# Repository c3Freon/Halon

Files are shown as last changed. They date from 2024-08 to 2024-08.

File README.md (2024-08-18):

# Halon 3D-Printer
## What is Halon
Halon is my 3D-Printer design. Its an small self containt portable high speed FDM 3D-Printer.
I designed this priter to be my travel printer for events and as an rabbit prototyping printer.

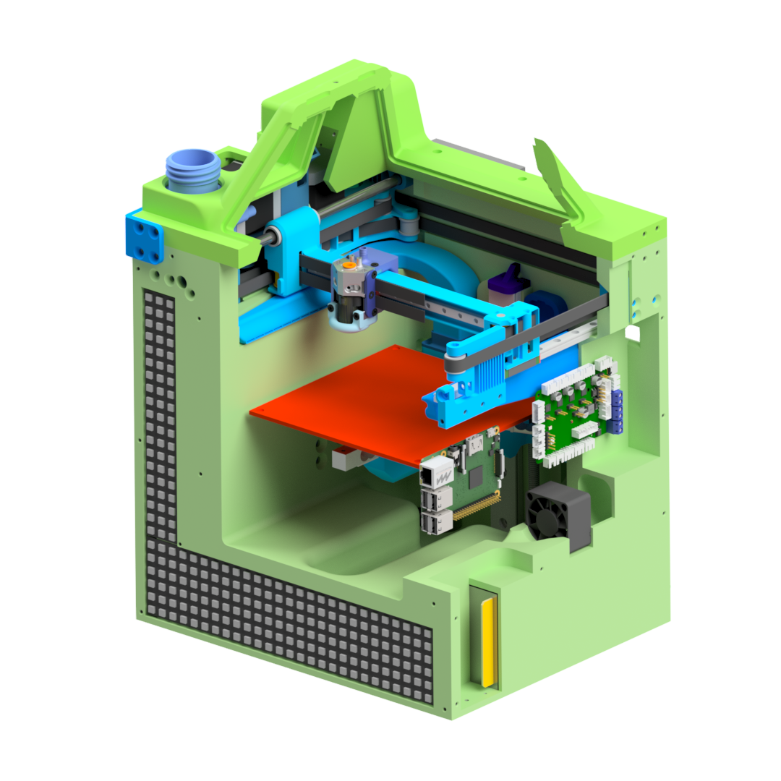
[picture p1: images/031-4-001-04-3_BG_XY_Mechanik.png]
3D-Render of the first Prototype


## Design Targets
1. The Printer should be usable as an praktical 3D-Printer
2. The Printer should be Self Containt. No external spool, no external power supply and an compleate printer enclosure.
3. The Printer should be as fast as possible. An design goal of 1m/s velocity and 100m/s² has been set.
4. The Printer should be buildable with standard mashiens avavible in moast Hackspaces/Makerspaces.

# Prototype
This Project started in autum 2023 as an studing project. I have developed the prototype over an halve jear and i build the prototype. On the GPN22 i presented the prototype. Because of the interest and feedback on the event, i decided to publish the design of printer so more people can build this design. 

https://github.com/user-attachments/assets/4c1e7ec1-202b-4d33-9429-380821325e8d

The mechanics of the prototype function as Planned. It reaches an maximum speed of 0.5m/s with an acceleration of 100m/s² reliable without stepp loss. Even at this high acceleration the ringing on the axis is minimal. 
The print cooling system is sufficient even on maximum print speed. But, the prototype uses two 15mm turbines for the side cooling and an compressor for the head part cooling. Both are extremly loud (operator needs ear protection when opening the enclosure) which violates the first design target.
The extrusion system is currently the speed limiting factor on this mashien. The prototype uses an Creality K1 Hotend and an dual gear browden extruder. Its currently limited to 30mm³/s. The hotend and the XY motors get cooled by an water cooling loop.

The Prototype was first designed to be mostly printed on the university SLS Printer. So some Parts arent optimised for more Accesseble Printing methodes. The hotend heatsink designed to be manufactured from aluminium with an SLM Printer.

Intermediate build state of the printer Where many aspects are visible and the cabeling horror hasnt begun

## Technical specifications
- Maximum speed 500mm/s at 100m/s² acceleration
- Print area 150x150x120mm
- Machine size 297x240x430mm
- Encapsulated print area
- Water cooled print head
- Acceleration sensor for input shaper
- Fillament spool integrated in printer
- Integrated active fillament drying box (maximum 70°C with fan)
- Charcoal filter with fan
- Auto-levelling via load cells under the print bed
- Rigid print bed
- Strong side cooling
- Rigid axle design for low ringing
- Klipper firmware
- Clog-free Y-axis guide

## Electronics
Two Bigtreetech skr pico control boards, two Raspberrypi picos and a Raspberrypi 4 were used to control the prototype. Two Bigtreetech TMC5160T Plus driver boards with a supply voltage of 48V were used for the stepper motors. A used server power supply was used as the power supply, providing 12V with a maximum output of 450W. Two boost converters are used to generate a 24V and a 48V rail from the 12V power supply. The first skr Pico control board is powered by the 24V and drives the stepper motors for the E and Z axes. It also drives the hot end heaters and some of the fans. The second SKR Pico control board is supplied with 12V. This board controls the heating bed and the drying box heating. The 48V stepper motor drivers are controlled by the first Rasperrypi Pico. The second pico is not connected to the Klipper. It reads the load cells under the bed and simulates a BL-Touch for automatic bed levelling to the controller.

## What works well
The printer's motion system works as designed. The printer achieves a positioning speed of 0.5m/s with an acceleration of 100m/s². The rigid axis structure means that even at these extreme settings, ringing is very low.
The cantilevered Z-axis is very rigid due to the rigid guide and wide beam.
Automatic levelling via load cells under the print bed is reliable and accurate.
The printer setup with a large print enclosure works.

https://github.com/user-attachments/assets/8164ebac-18e3-453c-8e3b-d6f8cc71612e

## What is still bad
A few problems were discovered with the first prototype. Firstly, water cooling will not be installed in future versions. The improved printhead cooling provided by water cooling does not justify the significantly increased maintenance and space requirements of water cooling. On the one hand, the cooling water has to be refilled every few days if silicone hoses are used. On the other hand, the tightness of the system is a problem. My prototype is currently leaking because the water tank has cracked due to the high pressure chamber temperatures.
Secondly, the extrusion system of the current printer is still suboptimal. In the prototype, the filament tube is bent too tightly in some places, causing high friction in the filament tube. In addition, the extruder cuts through the fillament when overloaded, which still happens too often due to the high friction in the system. 
The hot end is the limiting factor for print speed in the prototype.
When I designed the electronics, I didn't know about the Bigtreetech Kraken board. This would have simplified the electronics considerably. 
The side cooling fans can effectively cool the print even at maximum speed. However, the fans are so loud at maximum speed that ear protection is required next to the machine. The same applies to the compressed air cooling of the parts. This uses a piston compressor. However, this has a very high pressure pulsation, which also makes it very loud.
In addition, the heat generated by the stepper motors and voltage converters was underestimated during the design phase, which meant that fans had to be added to the prototypes at a later stage.

# Version 2
In the second version of the Halon printer I would like to fix the bugs of the first version. The following optimizations are planned:
- Replacing the water cooling of the print head with compressed air cooling (less maintenance)
- Upgrading the print head to a Mellow Goliath (higher volume flow)
- Modification of the extruder design (higher reliability, i have an high grip three wheel extuder design in the works)
- Use of a CPap fan for part cooling (noise reduction)
- Use of large radial fans for additional cooling (noise reduction)
- Modification of the control board to a Bigtreetech kraken
- Optimization of the housing design (improved assembly)

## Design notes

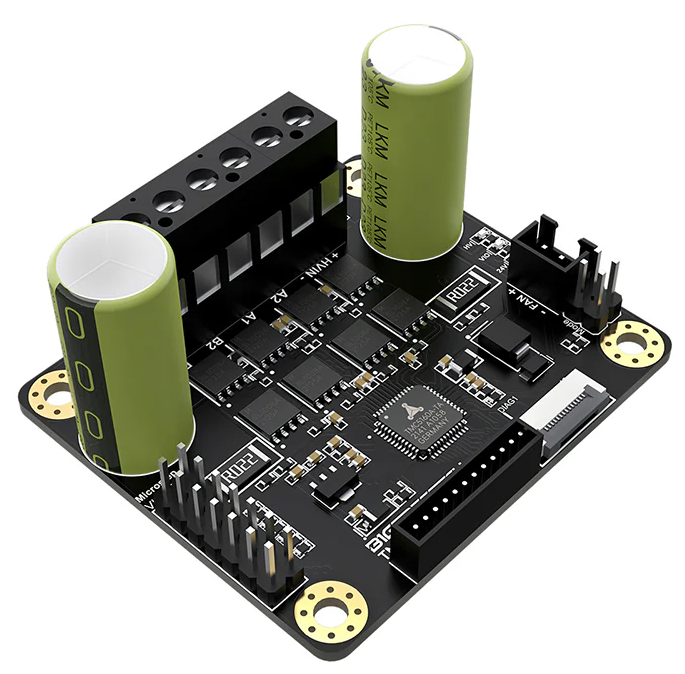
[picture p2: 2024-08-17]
images/Wiki/03_Pictures/08_MotorDriver.png

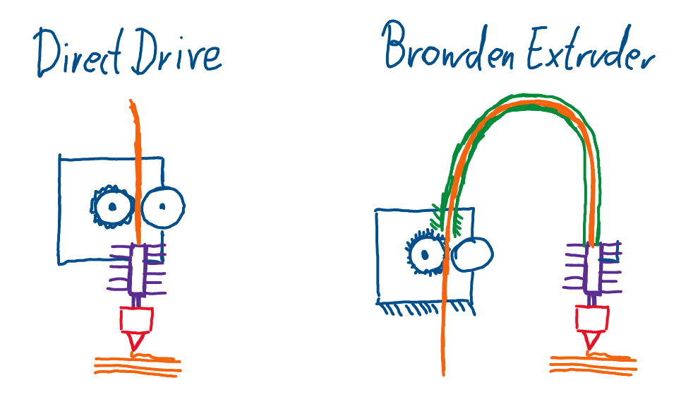
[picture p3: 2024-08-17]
images/Wiki/01_Skizzen/Extruder_Typen_01.png

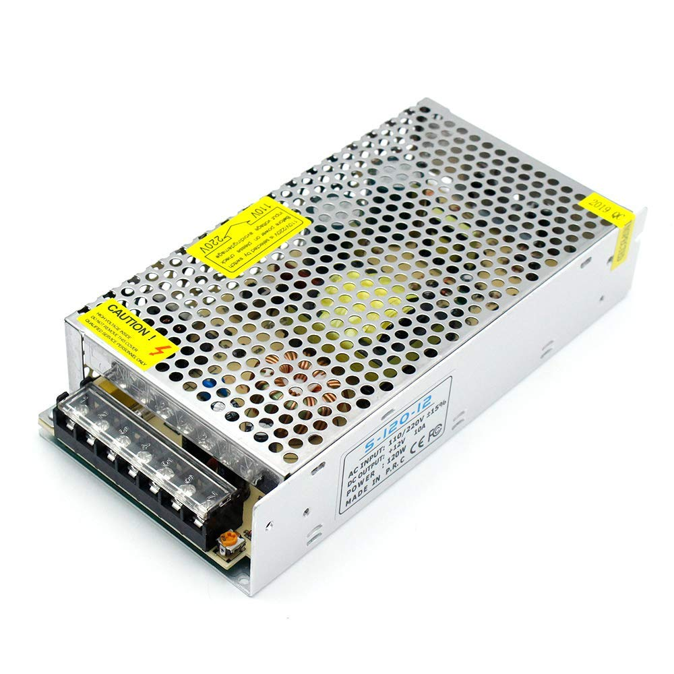
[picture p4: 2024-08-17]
images/Wiki/03_Pictures/00_Druckernetzteil.png

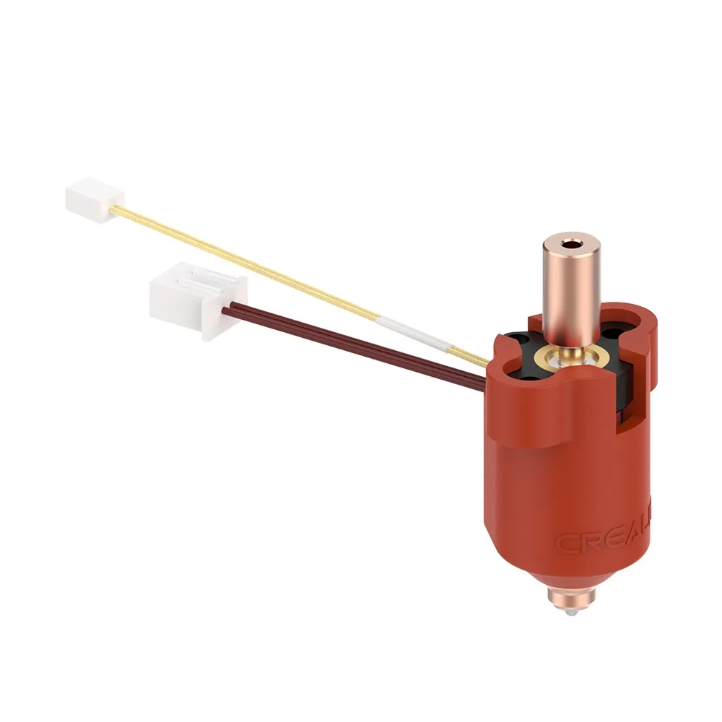
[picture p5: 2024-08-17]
images/Wiki/03_Pictures/03_Creality_Hotend.png

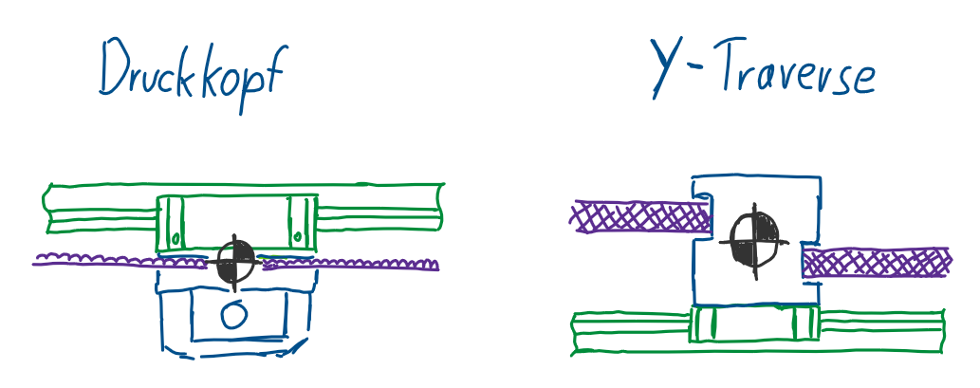
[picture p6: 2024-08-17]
images/Wiki/01_Skizzen/Schwerpunktslage_01.png

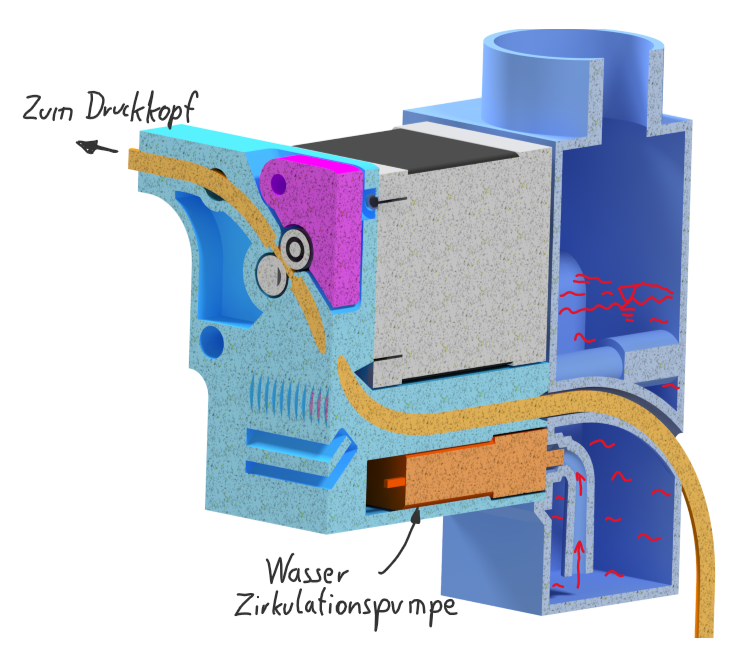
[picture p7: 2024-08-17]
images/Wiki/02_CAD_Pictures/Extruder_Filamentpfad_01.png

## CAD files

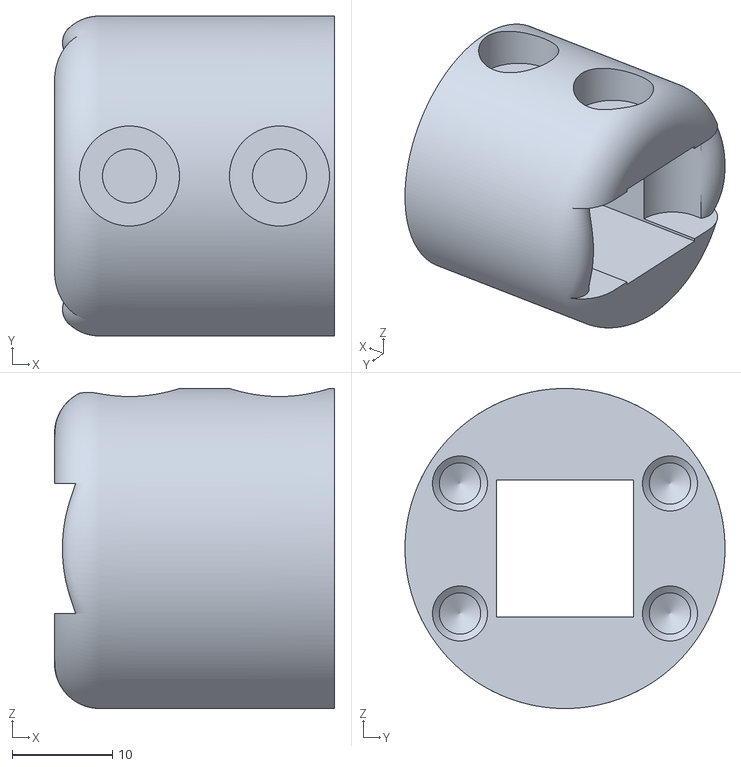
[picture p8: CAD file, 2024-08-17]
Version_01/FDM_Parts/031-5-029-00-5_01_Spulenhalter_Waegezellen Halter.stl
28.0 x 32.0 x 32.0

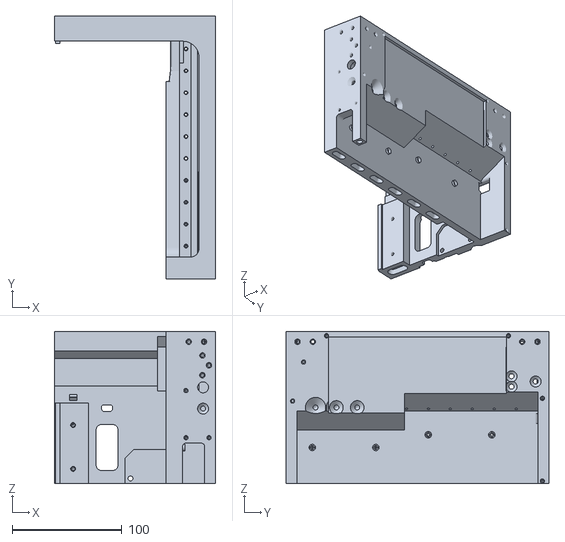
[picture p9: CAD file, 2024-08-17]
Version_01/FDM_Parts/Frame_for_BambuX1C/Gestell_Slice_Oben_Rechts.stl
147.0 x 240.0 x 139.0

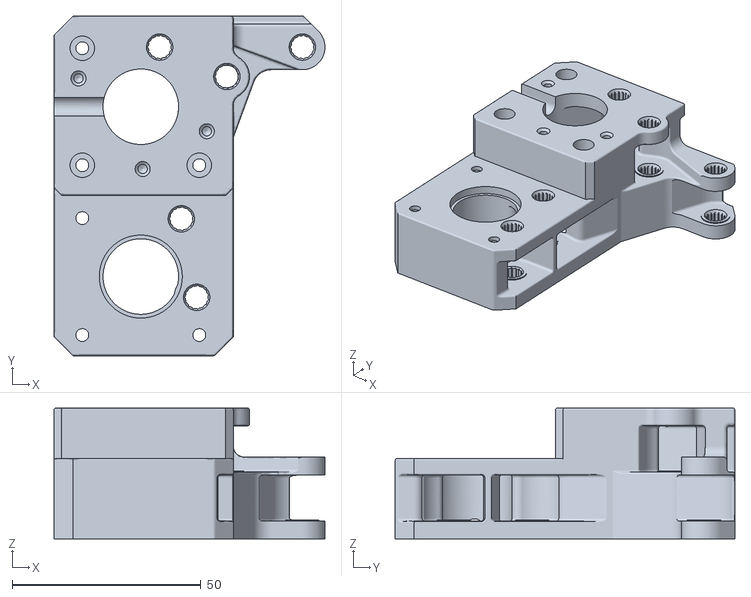
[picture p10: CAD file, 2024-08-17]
Version_01/SLA_Parts/031-5-016-01-5_00_Halteblock_1.stl
71.8 x 90.0 x 34.7

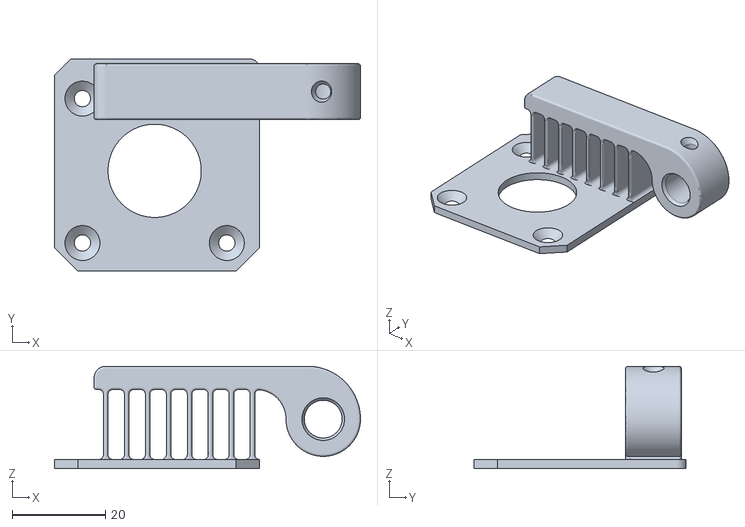
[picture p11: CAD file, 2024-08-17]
Version_01/SLS-SLM_Parts/031-5-016-00-5_01_Stangenhalter.stl
65.7 x 45.5 x 22.0

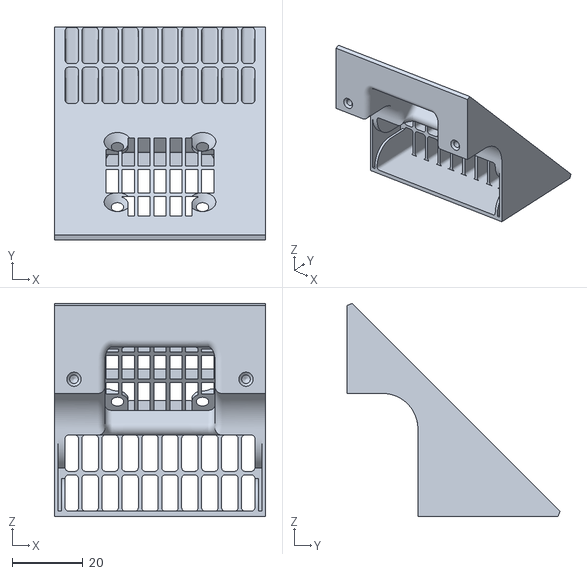
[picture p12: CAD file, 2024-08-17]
Version_01/FDM_Parts/031-5-025-00-3_Filament_Trockner.stl
59.5 x 60.1 x 60.1

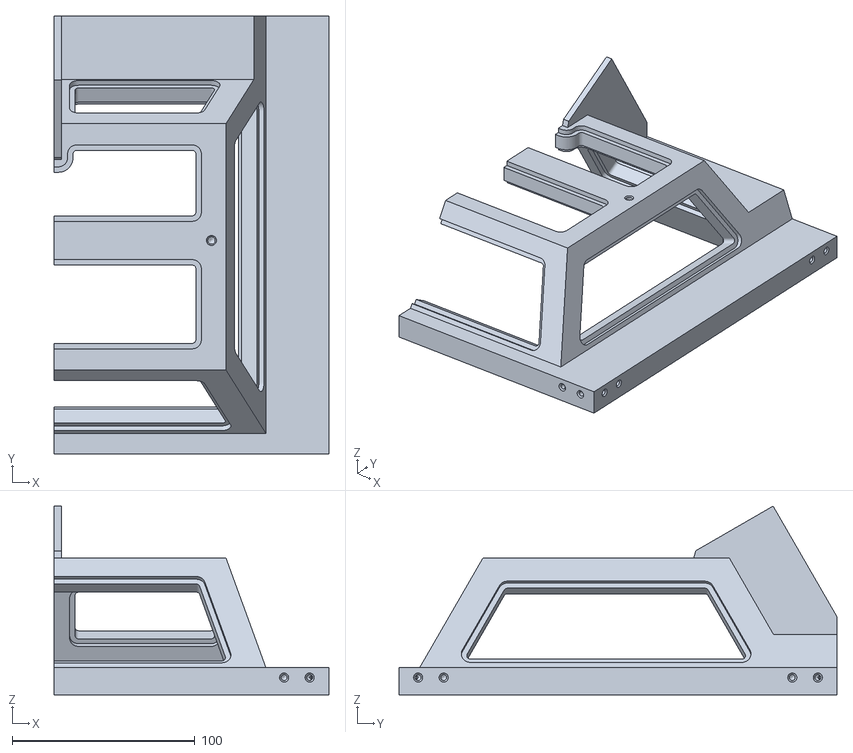
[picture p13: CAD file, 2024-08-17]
Version_01/FDM_Parts/Frame_for_BambuX1C/Dach_Rechts.stl
150.5 x 240.0 x 103.5

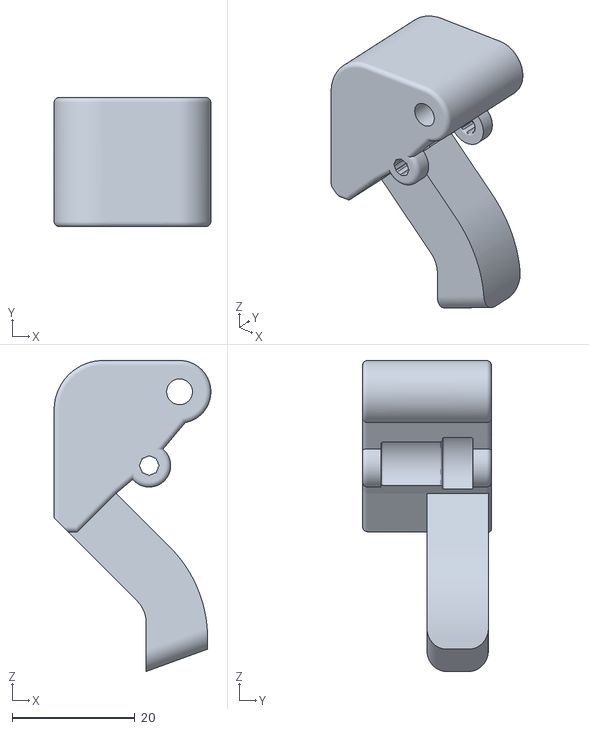
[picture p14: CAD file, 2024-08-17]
Version_01/SLA_Parts/031-5-011-03-5_01_Idler_Hebel.stl
25.5 x 21.0 x 50.7

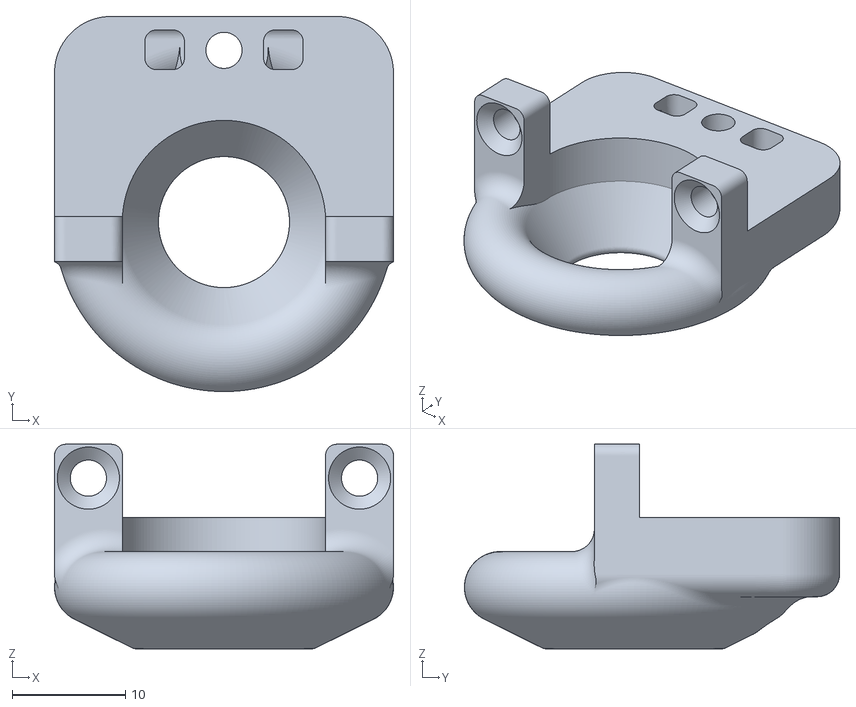
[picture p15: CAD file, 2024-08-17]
Version_01/SLS-SLM_Parts/031-5-012-03-5_05_Blasdüse.stl
30.0 x 33.2 x 18.1

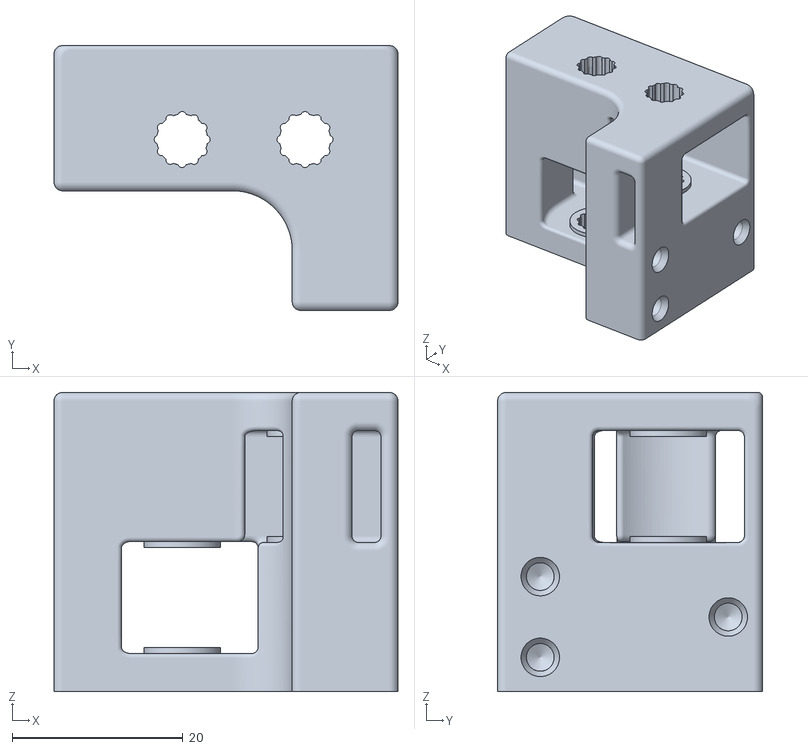
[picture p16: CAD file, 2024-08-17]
Version_01/FDM_Parts/031-5-020-01-3_Umlenkrollen_Halter_Hinten_Rechts.stl
40.3 x 31.0 x 35.0

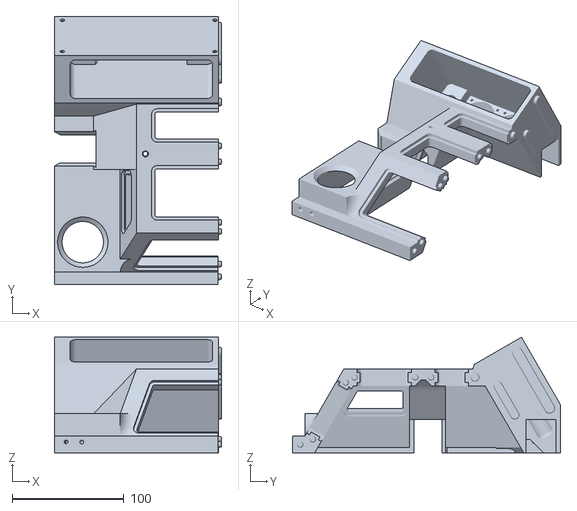
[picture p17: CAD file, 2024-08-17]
Version_01/FDM_Parts/Frame_for_BambuX1C/Dach_Links.stl
149.4 x 240.0 x 103.5

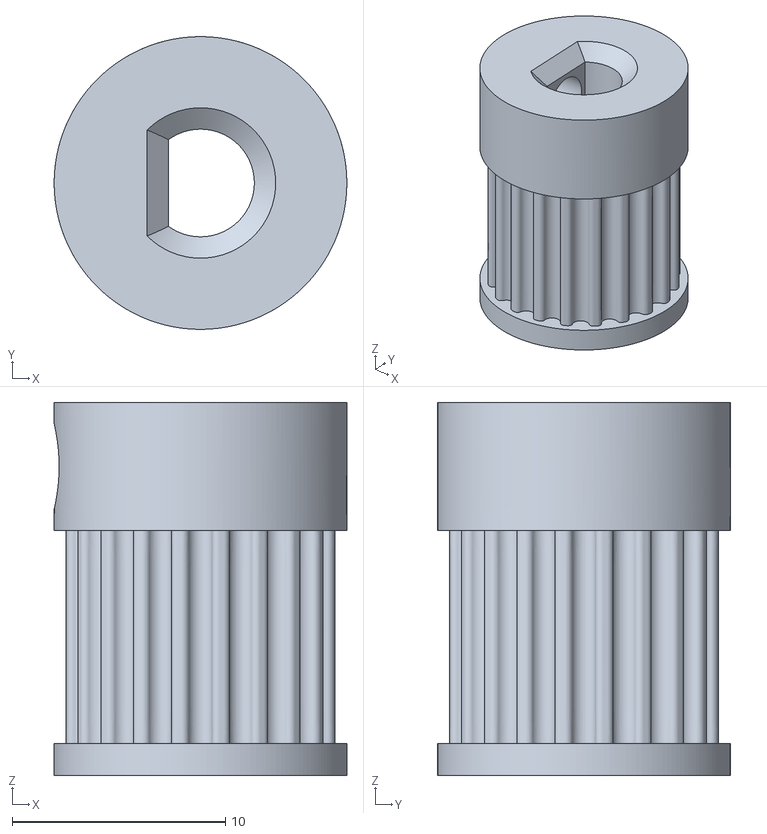
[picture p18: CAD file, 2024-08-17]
Version_01/SLA_Parts/031-5-015-01-3_Riemen_Pulley.stl
13.7 x 13.7 x 17.5

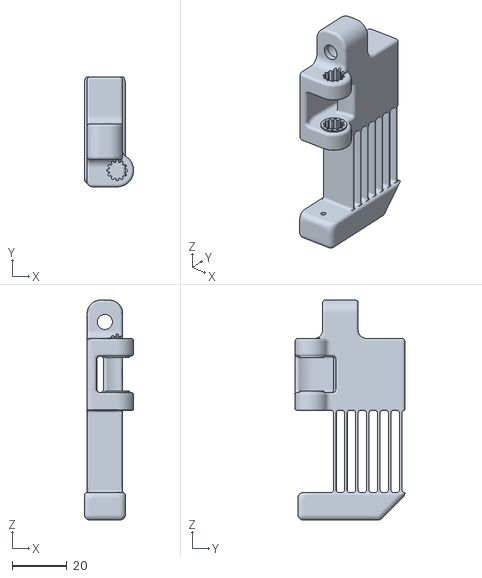
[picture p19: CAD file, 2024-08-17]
Version_01/SLS-SLM_Parts/031-5-021-01-3_Umlenkrollen_Halter_Vorne_Links.stl
18.0 x 40.0 x 80.2

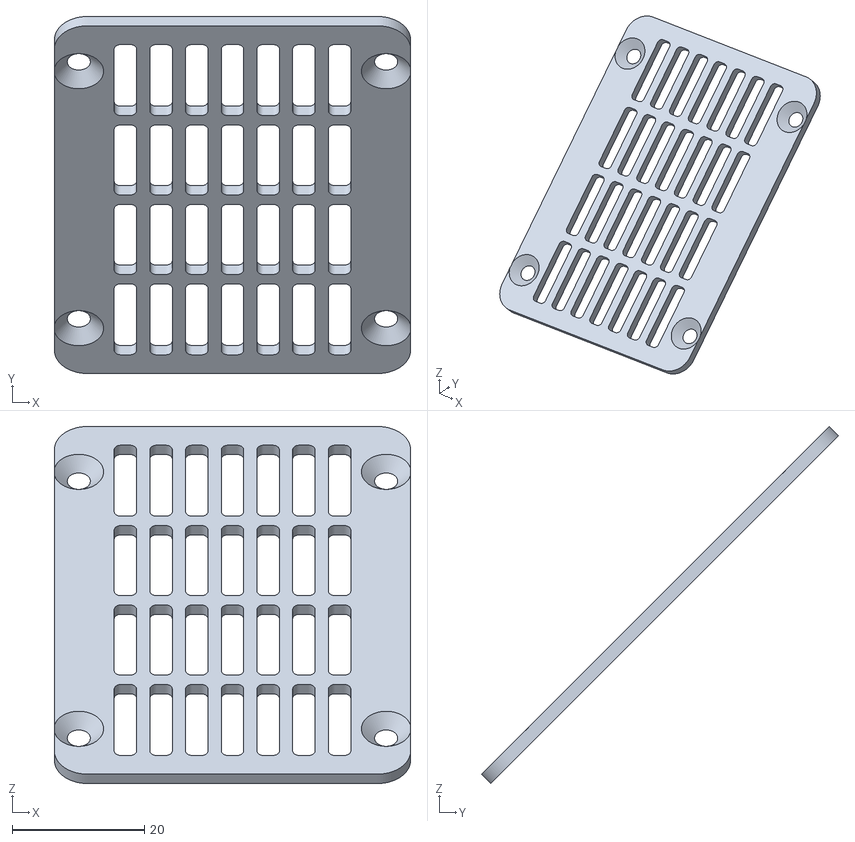
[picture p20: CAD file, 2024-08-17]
Version_01/FDM_Parts/031-5-026-00-5_01_Lufttrockner_Deckel.stl
53.9 x 54.0 x 54.0

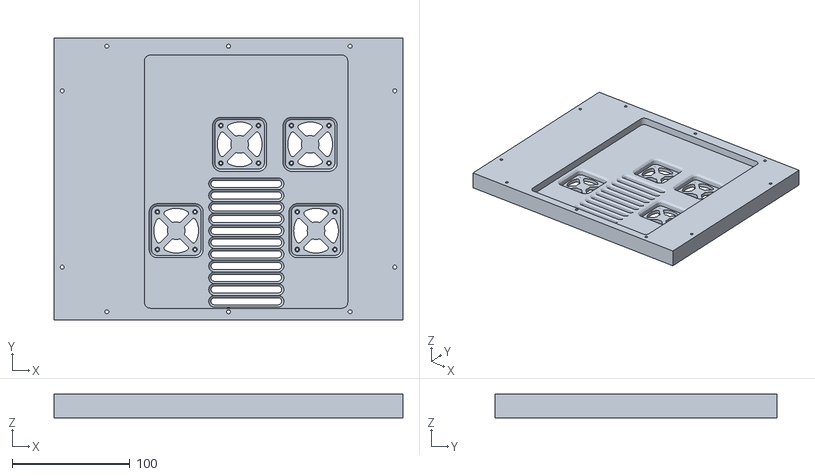
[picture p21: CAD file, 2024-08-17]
Version_01/FDM_Parts/Frame_for_BambuX1C/031-5-006-00-3_Gehäuse.stl
297.0 x 240.0 x 20.0

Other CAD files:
Version_01/SLA_Parts/031-5-023-00-5_01_Lüftertrichter.stl
Version_01/SLS-SLM_Parts/031-5-012-03-5_04_RückPlatte.stl
Version_01/FDM_Parts/031-5-019-00-3_Riemenspanner_Vorne_Rechts.stl
Version_01/FDM_Parts/Frame_for_BambuX1C/Gestell_Slice_Unten_Rechts.stl
Version_01/FDM_Parts/031-5-004-05-3_Druckbett_Träger.stl
Version_01/FDM_Parts/031-5-006-00-B_Gehäuse_Dach.stl
Version_01/FDM_Parts/031-5-009-02-5_00_Blasdüse_Links.stl
Version_01/FDM_Parts/031-5-009-03-5_01_Blasdüse_Rechts.stl
Version_01/FDM_Parts/031-5-023-00-5_00_Lüfterhalter.stl
Version_01/FDM_Parts/031-5-026-00-5_00_Lufttrockner_Gehäuse.stl
Version_01/FDM_Parts/031-5-029-00-5_00_Spulenhalter_Zapfen.stl
Version_01/FDM_Parts/031-5-031-00-5_00_Endschalter_Schieber.stl
Version_01/FDM_Parts/031-5-031-00-5_01_Endschalter_Schiene.stl
Version_01/FDM_Parts/031-5-032-00-3_Z-Stopper.stl
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

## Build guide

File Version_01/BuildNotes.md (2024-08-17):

# Read this beofore Replicating

Aktuell kann ich nicht empfehlen diesen Drucker nachzubauen. Während der Montage des Prototypen musste ich viele modifikationen an den Teilen vornehmen die ich nicht in den CAD Daten dokumentiert habe. Diese Daten sind fiel mehr als Referenz für weitere Druckerdesigns geeignet.

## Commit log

2024-08-16 Prototype Description
2024-08-17 Added the Prototype Parts
    Added the STL Parts of the first Prototype
    [031-5-004-05-3_Druckbett_Träger.stl, 031-5-006-00-3_Gehäuse.stl, 031-5-006-00-5_03_Dachhalter.stl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]
